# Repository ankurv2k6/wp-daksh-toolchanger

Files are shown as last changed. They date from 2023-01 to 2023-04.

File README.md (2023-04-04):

# WP-DAKSH 3D Printed Tool Changer

'WP-DAKSH' 3D Printed Tool Changer is a fully 3D printed tool changer compatible  with different CoreXY platforms like the Voron Trident, 1.8, 2.4  and RatRig VCore 3. 

It features state of the art advanced features including: 

  * Reliable tool changing mechanism powered by a single servo
  * Servo Burnout protection for enhanced life and efficient tool changes
  * Intelligent Error State Detection and Recovery minimizing failed prints
  * Automatic XYZ calibration across the different tools
  * Ultra Fast tool changing times of approx. 10 seconds - including nozzle cleaning and priming.
  * Capable of High accelerations and print speeds
  * Minimal loss in build space with the tool changer addition
  * Integrated nozzle cleaning mechanism for clean prints without the need for a purge tower / ooze shield
  * 4x4 LED Display on toolhead to display the current state of toolhead
  * Custom Klipper configuration, modules and macros for an integrated software package
  * Stiff Wire Looms and recoil management like Prusa XL - wire looms are entirely contained within the printer frame itself.
  *  Fully Enclosed Design in the same design ethos as the original Voron Trident design - giving it the ability to print high temp materials like ABS, PA6-CF and PC-CF etc which require enclosed chambers.

The design is open source and can be used freely for non commercial purposes. Do join the discord group at the link below and subscribe to the Youtube channel for more updates and interesting projects like this.

* Github - https://github.com/ankurv2k6/wp-daksh-toolchanger
* WP-Daksh Discord - https://discord.gg/Kz9VC8rWPg
* Initial BOM - https://docs.google.com/spreadsheets/d/12ISdJoCqgUTPsUwRrQ3VZWM-GBWw20C0cgHo7VGqMWU

Build Log and Demo videos 

https://www.youtube.com/channel/UCr8K1tva2CaEhyqNyaEjq_w

* Part 1 - Design Overview, Locking Mechanism & Multi Platform Compatibility
* Part 2 - Frame Overview & Carriage Assembly with Tool Locking Mechanism
* Part 3 - Assembling a tool - Dragon and V6 Hotend
* Part 4 - Putting it all together - carriage, tool, dock and their alignment 
* Part 5 - Wiring Overview - wire looms & ptfe management
* Part 6 - Electronics and Wiring management
* Part 7 - Software Setup & Initial Configuration
* Part 8 - Printing in multi material with the tool changer.

IMPORTANT INFO

Supports Needed for the following parts:

* Tools - STL/tools/v6/v6_front.stl, STL/tools/dragon/dragon_front.stl
* Dock -  STL/dock/dock_mount_left.stl, STL/dock/dock_mount_right.stl, STL/dock/dock_mount_middle.stl

Intelligent Error State Detection and Recovery Demo - https://www.youtube.com/watch?v=iPQEkaGzjxA&t=93s

Automatic XYZ Multi Tool Calibration Demo - https://www.youtube.com/watch?v=ppcTm3NfDo0

Sample Prints

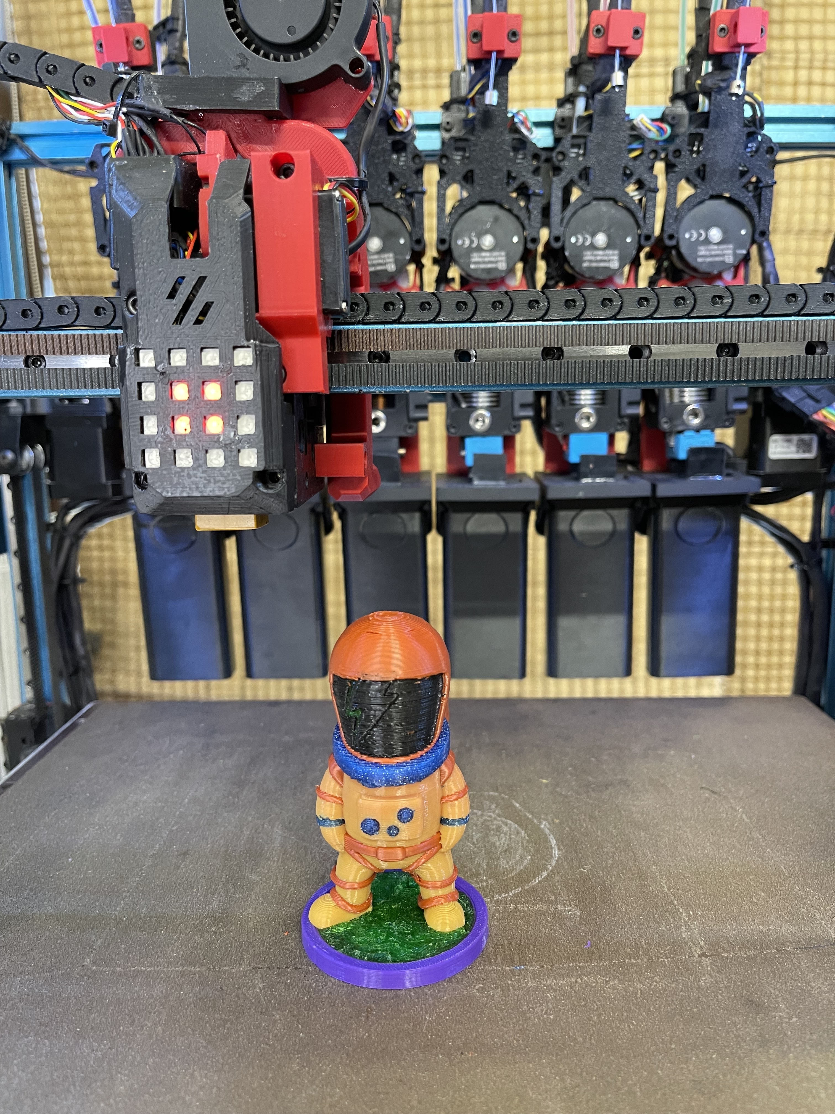
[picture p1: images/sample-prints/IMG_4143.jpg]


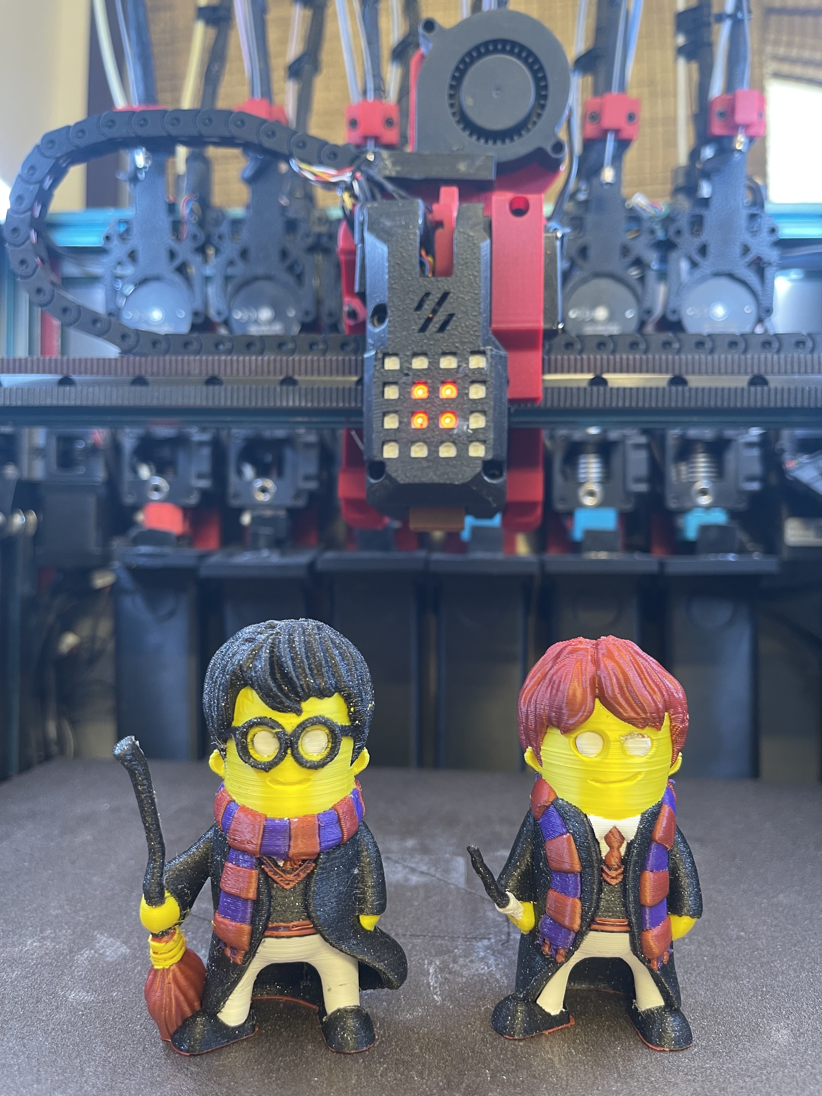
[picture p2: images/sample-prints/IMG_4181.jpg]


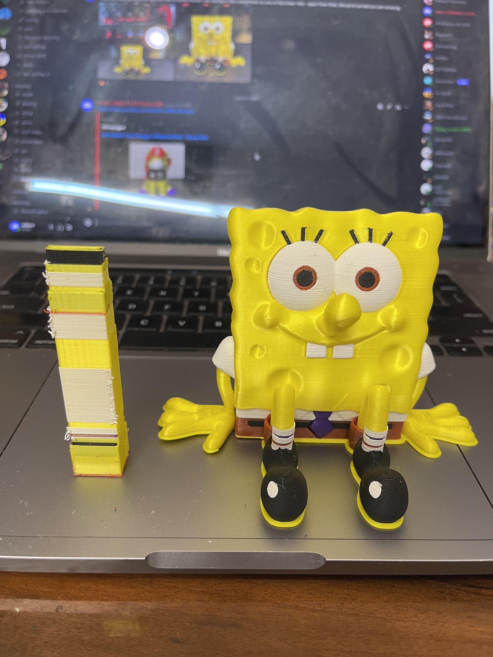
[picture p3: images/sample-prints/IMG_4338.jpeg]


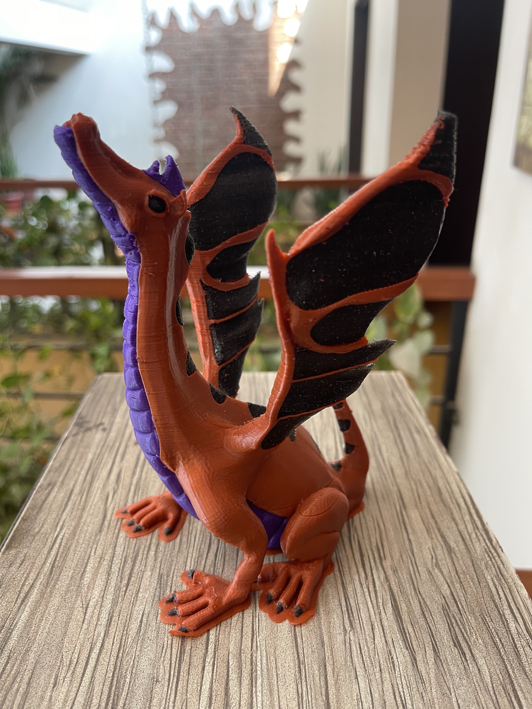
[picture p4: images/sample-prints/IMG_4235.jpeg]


Build Images

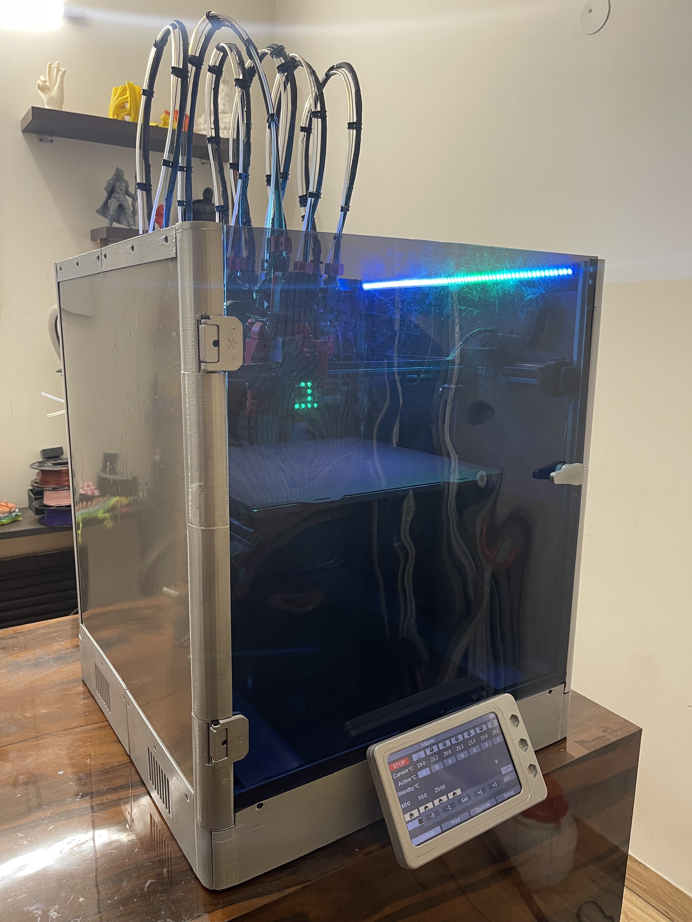
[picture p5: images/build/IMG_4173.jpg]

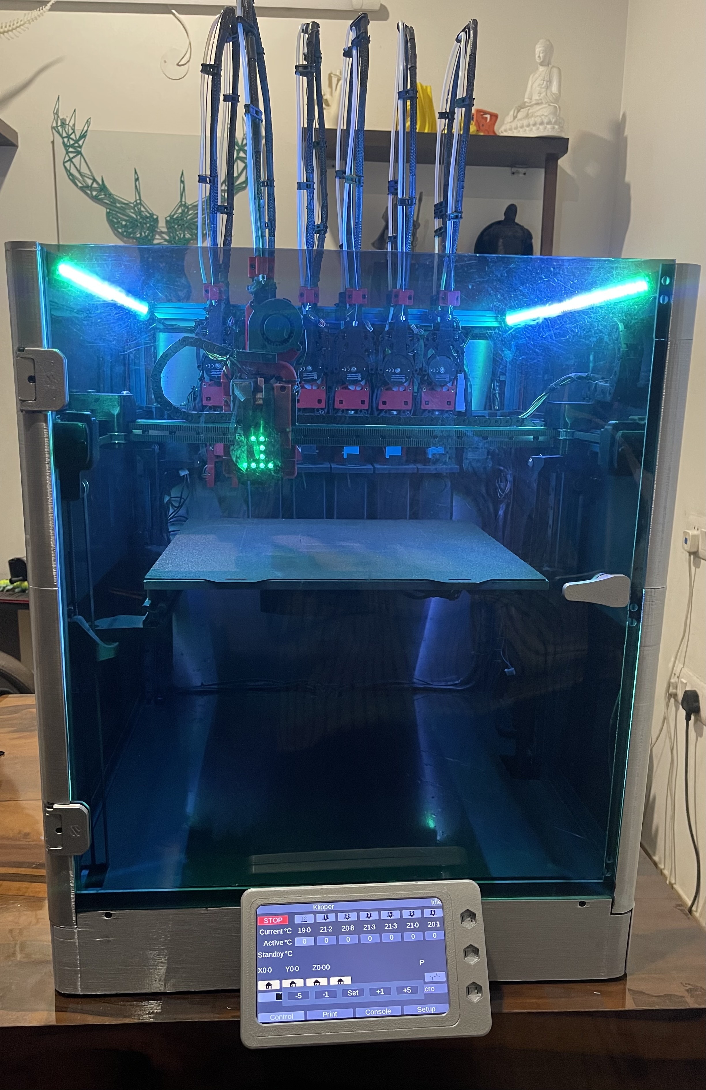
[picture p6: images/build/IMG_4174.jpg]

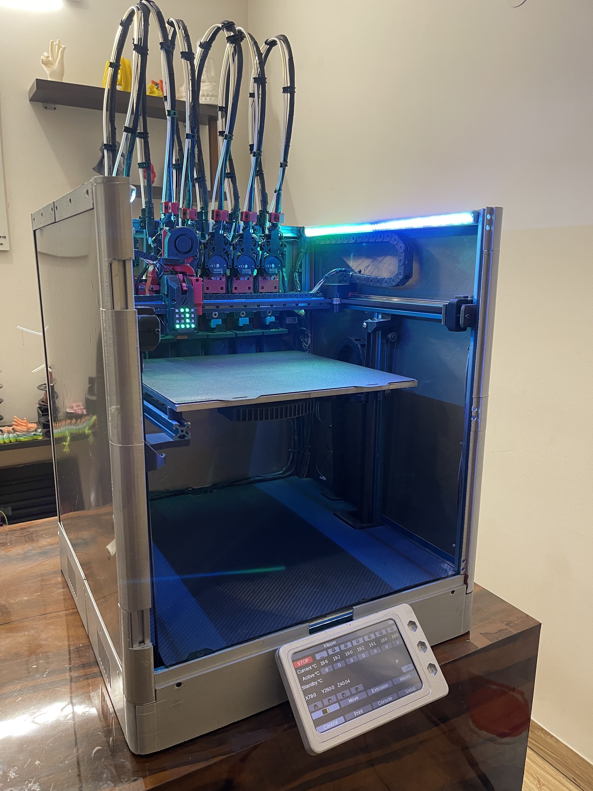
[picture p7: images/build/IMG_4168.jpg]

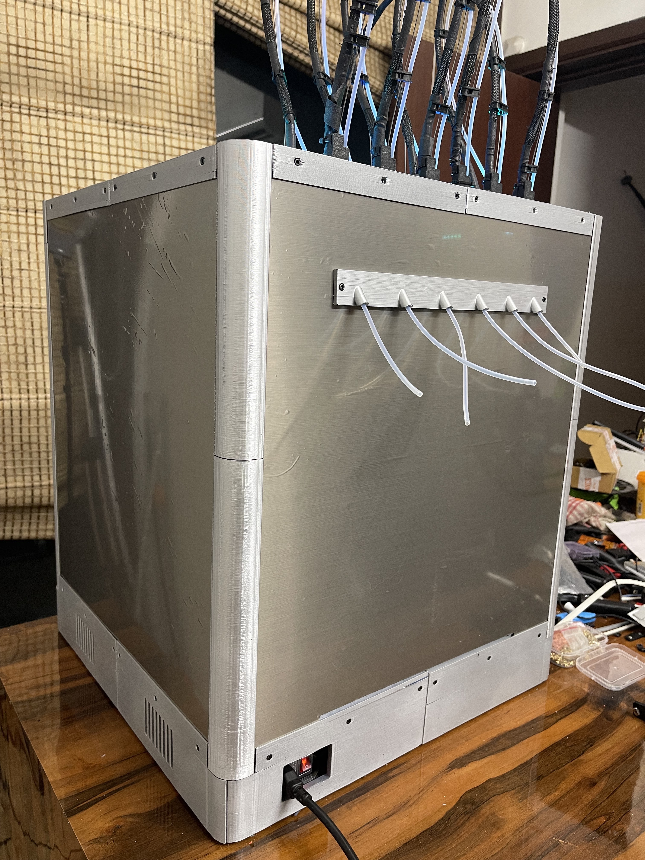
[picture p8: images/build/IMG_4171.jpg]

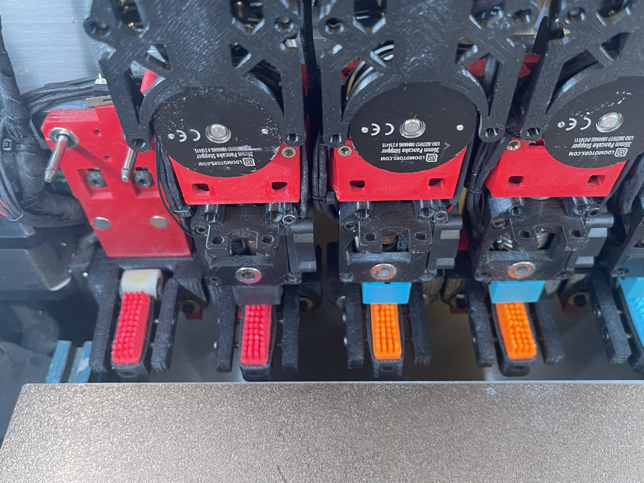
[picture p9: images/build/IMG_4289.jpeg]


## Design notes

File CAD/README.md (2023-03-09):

# WP-DAKSH 3D Printed Tool Changer - CAD Models

CAD Models are being provided due to the excellent effort of @edcasati who took it upon to convert the STLs from Tinkercad into a viable Fusion 360 Model. It might not be perfect - but its an excellent start for anyone who wants to modify the WP-DAKSH tool changer to fit their system.

Many Thanks @edcasati - really appreciate the effort.

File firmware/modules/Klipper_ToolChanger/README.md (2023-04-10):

Note: probe_multi_axis.py and atc_switch.py were dervied from the excellent work done here - https://github.com/ben5459/Klipper_ToolChanger/blob/master/probe_multi_axis.py

# Tools for klipper

This are python extras, macros and example config for the
[Klipper 3D printer firmware](https://github.com/Klipper3d/klipper). I
originally created this as macros when converting my Jubilee based
toolchanger from RRF and Duet3 to Klipper.

I welcome all contribution!

This is working great but treat it as a Beta version in development.

## Features

* **Each Tool is treated as an object and has it's own configuration** -
having configurable coordinates for parking, zoning, tool offset, 
meltzonelength, extruder, fan, etc.
*  **Multiple tools can be grouped in ToolGroup.** -Most configuration can
be inherited from the group if not specified in the tool config section.
*  **Virtual tools** - A tool can be virtual andhave a physical parent,
inheriting all nonspecified configuration from parent, parent group and
then toolgroup. Use case example of an ERCF on a PLA tool,a ERCF on a 
PETG tool, one tool without virtual tools for abrasive and yet another
tool with 3 markers that can switch between 3 markers by rotation.
* **Tools don't need to be extruders/hotends**, can be anything.
* **User defineable macro to Lock / Unlock** - Uses custom gcodes in config 
like the gcode_button. This can call a macro or multiple lines. 
* **User defineable macro to Pickup / Dropoff tools** - Can be inherited.
In the macro, `myself` refers to the calling toolobject so you can get 
myself.id for tool number or myself.offset[0] for X offset in the macro.
Ex. having same pickup gcode macro inherited for all tools from a group 
except for one that uses another type of toolwipe and has it's own pickup_gcode.
* **Global ToolLock parameters** - example purge_on_toolchange can be set 
to false when aligning tools with TAMV/ZTATP.
* **Fan speed** is carried over on toolchange if the tool has a fan. Also
`M106`/`M107` defaults to current_tool to set fan speed but can also use a Pnnn 
parameter to specify another tool.
* **Extruder temperature control** - 
  - Definable for any tool with a Pnnn parameter or defaults to current_tool
  - Has diffrent Active and Standby temperatures.
  - Can be set in Active, Standby or Off mode.
  - Can have delayed Standby and Off. Configured and/or customized with N and O parameters at runtime.
    - Example. Set Standby temperature 30 sec after putting the tool in standby and in Off after 30 minutes of not being activated.
    - Or set Time to standby to 0.1 for instant standby and Time to Powerdown to 604800 for a having it powered for a week.
    - Usefull when having sporadic toolchanges in a large print or many toolchanges in a small print.
  - Wait to reach temperature with tolerance. Set temperature +/- configurable tolerance.
* Current Tool is saved and restored at powerdown. Default but optional.
* Input shaper parameters for each tool.
* Position prior to toolchange can optionaly be saved and restored.

## Installation Instructions
### Install with Moonraker Autoupdate Support
This plugin assumes that you installed Klipper into your home directory (usually `/home/pi`). 

1) Clone this repo into your home directory where Klipper is installed:
```
cd ~
git clone https://github.com/TypQxQ/Klipper_ToolChanger.git
```

2) Edit `moonraker.conf` by adding the following entry:
```
[update_manager client klipper_toolchanger]
type: git_repo
path: ~/Klipper_ToolChanger
origin: https://github.com/TypQxQ/Klipper_ToolChanger.git
install_script: install.sh
is_system_service: False
```

3) Run the `install.sh` script
```
~/Klipper_ToolChanger/install.sh
```

Klipper_ToolChanger will show up in the update the next time you restart moonraker, or you can restart mooraker right away with: `sudo systemctl restart moonraker`.
If you encouter errors after an automatic Klipper update you can safetly run the `install.sh` scipt again to repair the links to the extension.

### Manual Install
Copy the python (`*.py`) files into the `\klipper\klipper\extras` directory. Assuming Klipper is installed in your home directory:
```
cp ./*.py ~/klipper/klippy/extras/
```
Then restart Klipper to pick up the extensions.

## To do:
* Add virtual tools select code.
* Add selectable automatic calculation of active times based on previous times. Ex:
  * Mean Layer time Standby mode. - Save time at every layerchange and at toolchange set to mean time of last 3 layers *2 or at last layer *1.5 with a Maximum and a minimum time. Needs to be analyzed further.
  * Save the time it was in Standby last time and apply a fuzzfactor. Put tool in standby and heatup with presumption that next time will be aproximatley after the same time as last. +/- Fuzzfactor.
* Save pressure avance per tool to be restored on toolchange. Also between virtual tools. Check Slicer output first if this is needed or can be put in Filament custom gcode.

## Configuration requirements
* `[input_shaper]` needs to be used for input shaper to wordk.

## G-Code commands:
* `TOOL_LOCK` - Lock command
* `TOOL_UNLOCK` - Unlock command
* `Tn` - T0, T1, T2, etc... A select command is created for each tool. 
  * `R` - Calls SAVE_CURRENT_POSITION with the variable as a RESTORE_POSITION_TYPE. For example "T0 R1" will call "SAVE_CURRENT_POSITION RESTORE_POSITION_TYPE=1" before moving. Positioned is restored with "RESTORE_POSITION" from below.
* `T_1` - Dropoff the current tool without picking up another tool
* `SET_AND_SAVE_FAN_SPEED` - Set the fan speed of specified tool or current tool if no `P` is supplied. Then save to be recovered at ToolChange.
  * `S` - Fan speed 0-255 or 0-1, default is 1, full speed.
  * `P` - Fan of this tool. Default current tool.
* `TEMPERATURE_WAIT_WITH_TOLERANCE` - Waits for all temperatures, or a specified tool or heater's temperature.
This command can be used without any additional parameters. Without parameters it waits for bed and current extruder. Only one of either TOOL or HEATER may be used.
  - `TOOL` - Tool number.
  - `HEATER` - Heater number. 0="heater_bed", 1="extruder", 2="extruder1", 3="extruder2", etc. Only works if named as default, this way.
  - `TOLERANCE` - Tolerance in degC. Defaults to 1*C. Wait will wait until heater is between set temperature +/- tolerance.
* `SET_TOOL_TEMPERATURE` - Set tool temperature.
  * `TOOL` - Tool number, optional. If this parameter is not provided, the current tool is used.
  * `STDB_TMP` - Standby temperature(s), optional
  * `ACTV_TMP` - Active temperature(s), optional
  * `CHNG_STATE` - Change Heater State, optional: 0 = off, 1 = standby temperature(s), 2 = active temperature(s).
  * `STDB_TIMEOUT` - Time in seconds to wait between changing heater state to standby and setting heater target temperature to standby temperature when standby temperature is lower than tool temperature.
    * Use for example 0.1 to change immediately to standby temperature.
  * `SHTDWN_TIMEOUT` - Time in seconds to wait from docking tool to shutting off the heater, optional.
    * Use for example 86400 to wait 24h if you want to disable shutdown timer.
* `SET_GLOBAL_OFFSET` - Set a global offset that can be applied to all tools
  * `X` / `Y` / `Z` - Set the X/Y/Z offset position
  * `X_ADJUST` / `Y_ADJUST` / `Z_ADJUST` - Adjust the X/Y/Z offset position incramentally
* `SET_TOOL_OFFSET` - Set the offset of an individual tool
  * `TOOL` - Tool number, optional. If this parameter is not provided, the current tool is used.
  * `X` / `Y` / `Z` - Set the X/Y/Z offset position
  * `X_ADJUST` /`Y_ADJUST` / `Z_ADJUST` - Adjust the X/Y/Z offset position incramentally  
* `SET_PURGE_ON_TOOLCHANGE` - Sets a global variable that can disable all purging (can be used in macros) when loading/unloading. For example when doing a TAMV/ZTATP tool alignement.
* `SAVE_POSITION` - Sets the Restore type and saves specified position for the toolhead. This command is usually used inside the custom g-code of the slicer software. The restore_position_on_toolchange_type will be changed to reflect the passed parameters.
  * X= X position to save, optional but Y must be specifie or this will be ignored.
  * Y= Y position to save, optional but X must be specifie or this will be ignored.
  * Z= Z position to save, optional but X and Y must be specifie or this will be ignored.
    * With no parameters it will set Restore type to 0, no restore.
    * With X and Y parameters it will save the specified X and Y. Sets restore type to 1, restore XY.
    * With X, Y and Z parameters it will save the specified X, Y and Z. Sets restore type to 2, restore XYZ.
* `SAVE_CURRENT_POSITION` - Save the current G-Code position of the toolhead. This command is usually used inside the pickup_gcode script or the custom g-code of the slicer software.
  * RESTORE_POSITION_TYPE= Type of restore, optional. If not specified, restore_position_on_toolchange_type will not be changed.
    * 0: No restore
    * 1: Restore XY
    * 2: Restore XYZ
* `RESTORE_POSITION` - Restore position to the latest saved position. This command is usually used inside the pickup_gcode script.
  * RESTORE_POSITION_TYPE= Type of restore, optional. If not specified, restore_position_on_toolchange_type will be used.
    * 0: No restore
    * 1: Restore XY
    * 2: Restore XYZ
## Values accesible from Macro for each object
- **Toollock**
  - `global_offset` - Global offset.
  - `tool_current` - -2: Unknown tool locked, -1: No tool locked, 0: and up are toolnames.
  - `saved_fan_speed` - Speed saved at each fanspeedchange to be recovered at Toolchange.
  - `purge_on_toolchange` - For use in macros to enable/disable purge/wipe code globaly.
  - `restore_position_on_toolchange_type` - The type of restore position:
    - 0: No restore
    - 1: Restore XY
    - 2: Restore XYZ
  - `saved_position` - The position saved when the latest T# command had a RESTORE_POSITION parameter to other than 0
- **Tool** - The tool calling this macro is referenced as `myself` in macros. When running for example `T3` to pickup the physical tool, in `pickup_gcode:` of one can write `{myself.name}` which would return `3`.
  - `name` - id. 0, 1, 2, etc.
  - `is_virtual` - If this tool has another layer of toolchange possible.
  - `physical_parent_id` - Parent physical tool that holds tool coordinates. Can be same as this.
  - `extruder` - extruder name as configured.
  - `fan` - fan name.
  - `lazy_home_when_parking` - When set to 1, will home unhomed XY axes if needed and will not move any axis if already homed and parked. 2 Will also home Z if not homed.
  - `meltzonelength` - Meltzonelength to unload/load filament at toolpak. See e3d documentation.
  - `zone` - Fast aproach coordinates when parking
  - `park` - Parking spot, slow aproach.
  - `offset` - Tool offset.
  - `heater_state` - 0 = off, 1 = standby temperature, 2 = active temperature. Placeholder.
  - `heater_active_temp` - Temperature to set when in active mode.
  - `heater_standby_temp` - Temperature to set when in standby mode.
  - `idle_to_standby_time` - Time in seconds from being parked to setting temperature to standby the temperature above. Use 0.1 to change imediatley to standby temperature.
  - `idle_to_powerdown_time` - Time in seconds from being parked to setting temperature to 0. Use something like 86400 to wait 24h if you want to disable. Requred on Physical tool.
- **ToolGroup**
  - `is_virtual` - As above
  - `physical_parent_id` - As above
  - `lazy_home_when_parking` - As above

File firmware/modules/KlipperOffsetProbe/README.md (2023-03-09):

# KlipperOffsetProbe
A Klippy plugin which solves the problem (when paired with a removable hardware probe) of finding the Z-offset between multiple tools.

If you have a toolchanger or IDEX printer you probably find yourself having to manually set Z offsets from time to time, either when changing tools or changing nozzles.

This script will cycle through each tool and probe the nozzle on a hardware probe somewhere on the printer and report the difference between the nozzle and the standard Z limit switch for each tool.

## How's it work?
When `offset_probe` is called on the printer the script will:
- Home the Z limit switch on top of the probe to get a Z0 location
- Check the config for a toolchange command named `toolchange_gcode_<tool number>` where tool number is between 0 and 99
- Executes the specified ttolchange Gcode, then moves to (`probe_x`, `probe_y`) and performs a probe using the custom probe specified by `pin` config
- Calculates the difference between the trigger of the Z probe and the custom probe to determine offset

After probing each tool the final results will be logged in the console to be saved by you.
Since toolchanging has no standardised approach in the Klipper world this is an easier approach than making assumptions about any specific implementation.

## Config example

```yaml
[offset_probe]
# Define the pin that the extra probe is connected to
pin: ^PC16
# X,Y coordinates to probe - these should be the native coordinates before any offsets are applied
probe_x: 150
probe_y: 150
# Z offset of the Z limit switch, which will be added to the calculated offset
z_offset: 0
# Additional offset added to each determined tool offset to account for micro switch pre-travel
# e.g. when using a removable hardware probe that utilises a micro switch to trigger
switch_offset: 0
# The speed (in mm/sec) to move tools down onto the probe
speed: 5
# The speed (in mm/sec) to retract between probes
lift_speed: 5
# Distance to retract between probes - default of 0.5
lift_distance: 10
# The speed (in mm/sec) of X/Y moves - default of 100
move_speed: 100
# Gcode macro to be run before anything else happens. A good use might be to ensure no tools are attached
start_gcode:
    TOOL_DROPOFF
# Gcode macro to run after all tools are probed, for example to ensure all tools were parked
end_gcode:
    TOOL_DROPOFF
# Defines 3 tools to be probed. Note that they do not have to be sequential, you may skip tools if that's desirable
toolchange_gcode_0:
    T0
toolchange_gcode_1:
    T1
toolchange_gcode_2:
    T2
```

## Installation
The simplest maintainable approach is to clone this repo to your host and then link the script to the klippy folder:
```bash
git clone https://github.com/Xonman/KlipperOffsetProbe ~/KlipperOffsetProbe
ln -s ~/KlipperOffsetProbe/offset_probe.py ~/klipper/klippy/extras/offset_probe.py
```
This should allow you to pull updates to the script without having to copy/paste it into the klippy folder each time.

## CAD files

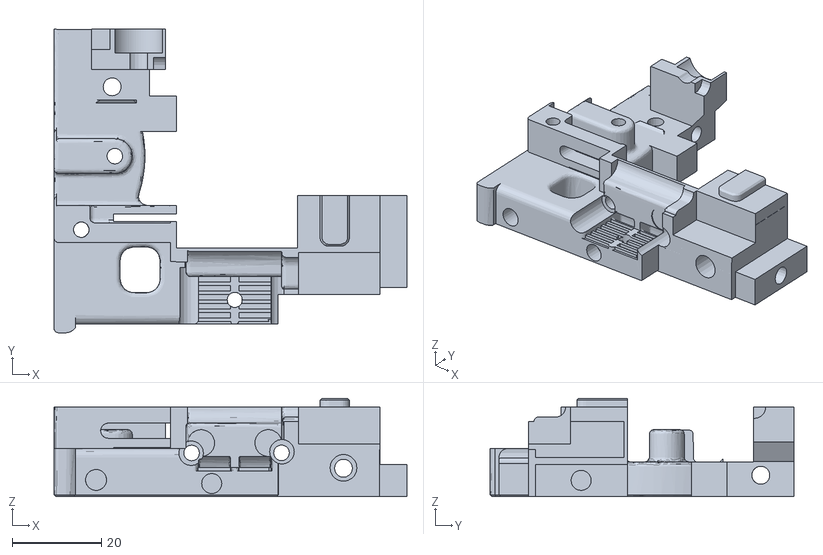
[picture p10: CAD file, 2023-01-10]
STL/carriage/carriage_right.stl
78.9 x 67.9 x 22.0

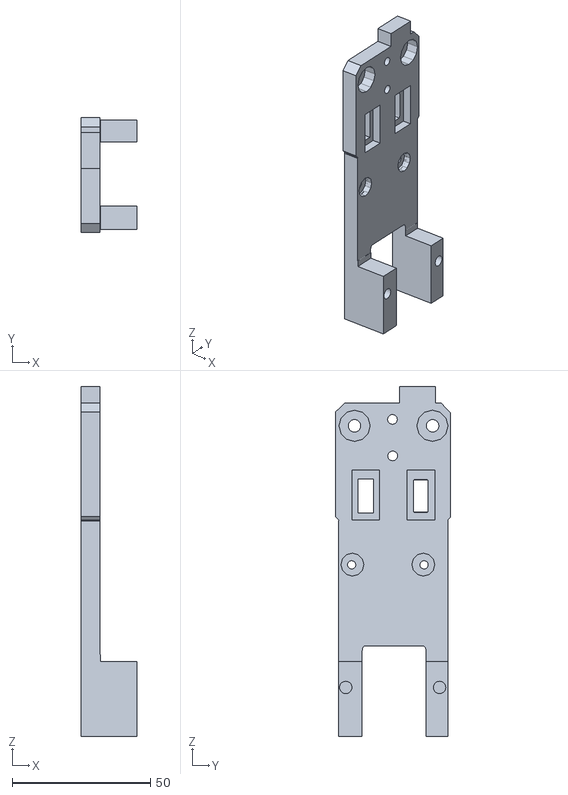
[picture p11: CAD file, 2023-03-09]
STL/dock/nozzle_wiper_mount.stl
20.1 x 41.7 x 126.6

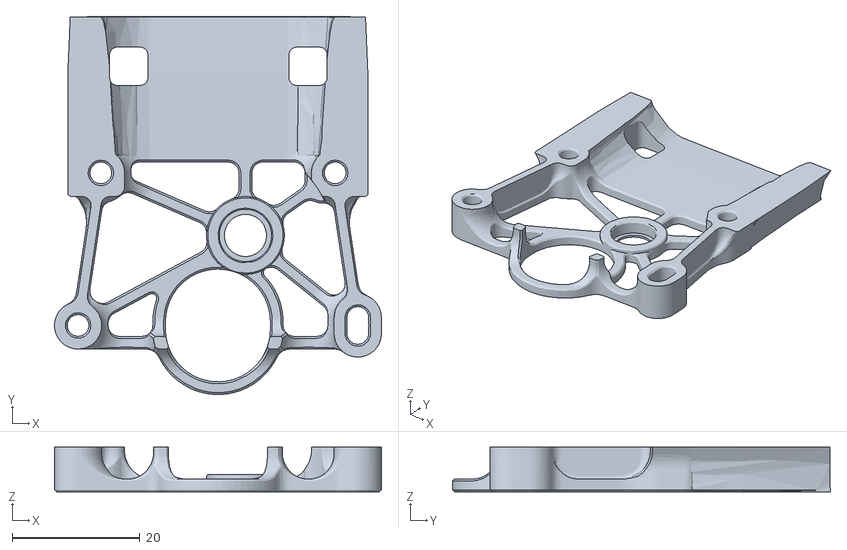
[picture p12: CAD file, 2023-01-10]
STL/extruder/extruder_back.stl
51.2 x 59.2 x 7.00

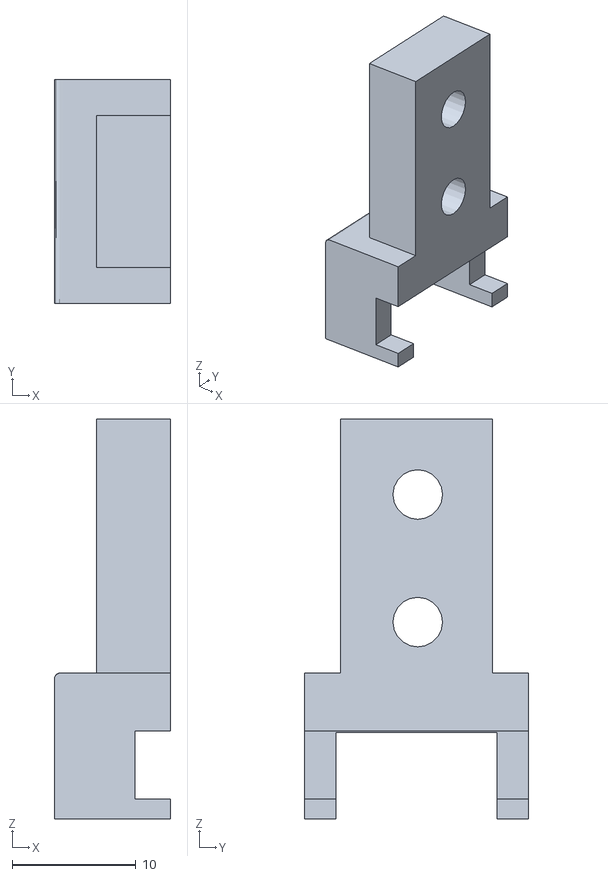
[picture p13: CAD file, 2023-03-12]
STL/front_idlers_25mm_extra_Y/y-endstop.stl
9.40 x 18.1 x 32.3

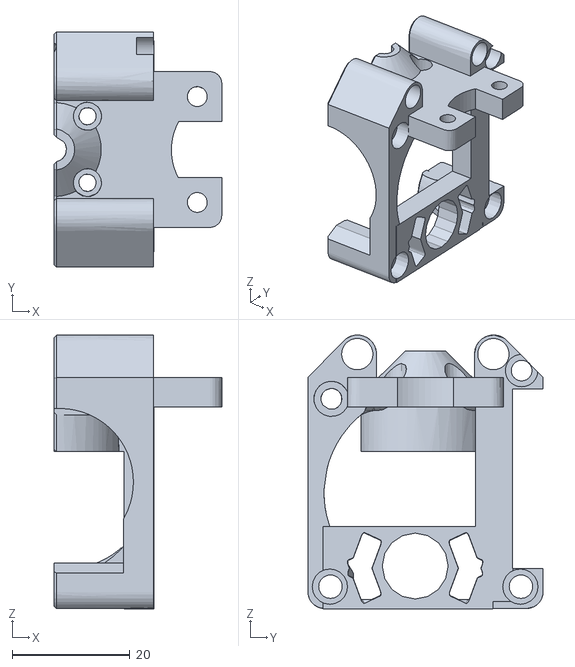
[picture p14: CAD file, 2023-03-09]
STL/tools/tool_dragon/dragon_front.stl
28.5 x 40.0 x 46.6

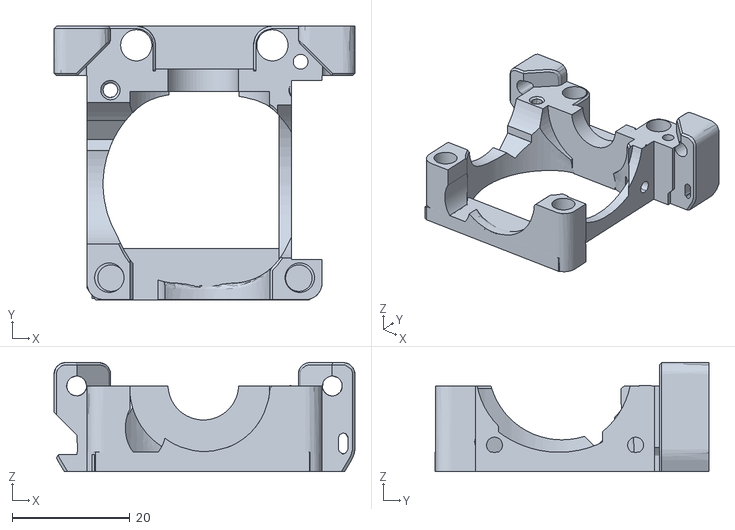
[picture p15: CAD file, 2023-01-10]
STL/tools/tool_v6/v6_back.stl
51.2 x 46.5 x 18.5

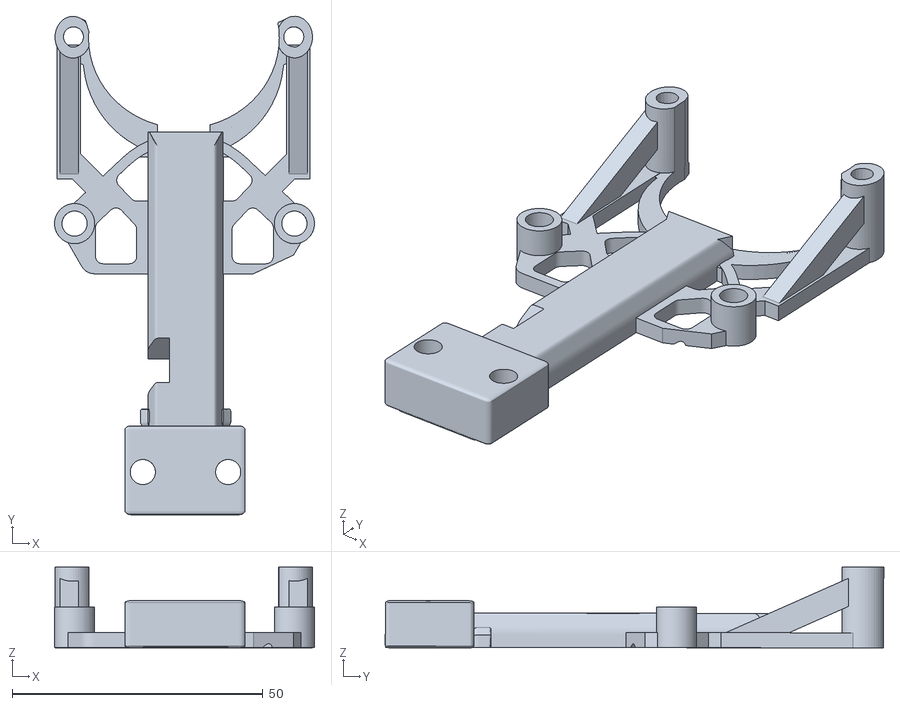
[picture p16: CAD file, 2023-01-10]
STL/umbilical/tool_umbilical_mount.stl
51.8 x 99.3 x 16.1

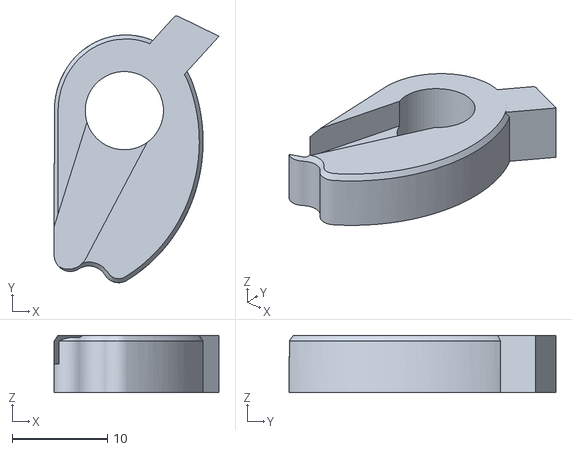
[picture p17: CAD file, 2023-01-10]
STL/carriage/servo_horn.stl
17.3 x 28.0 x 6.01

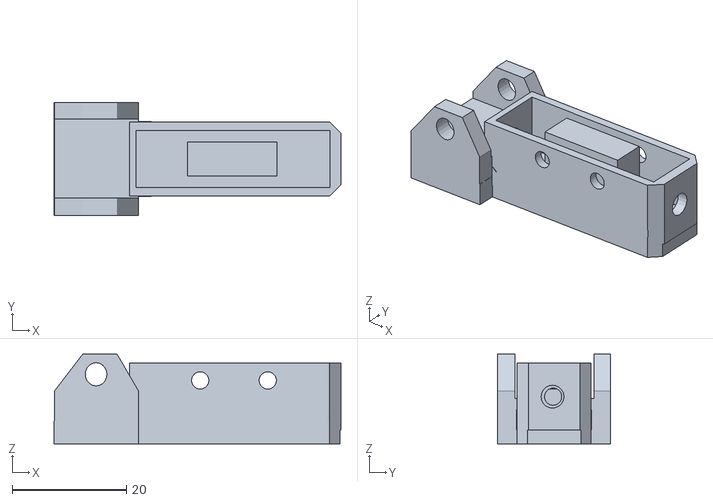
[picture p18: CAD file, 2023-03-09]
STL/dock/ooze_shield_nozzle_wiper.stl
50.1 x 19.8 x 15.7

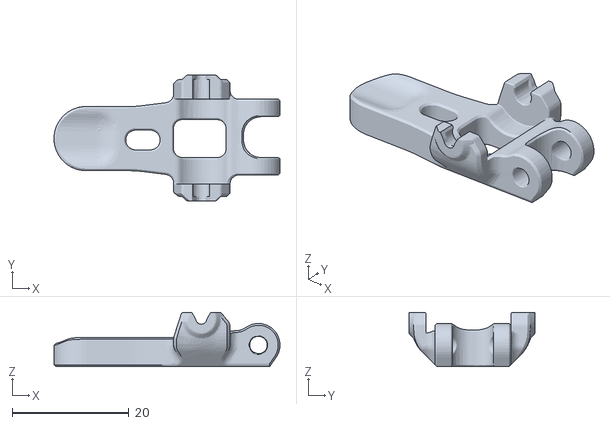
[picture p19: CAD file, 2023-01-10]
STL/extruder/extruder_idler.stl
38.7 x 21.6 x 9.30

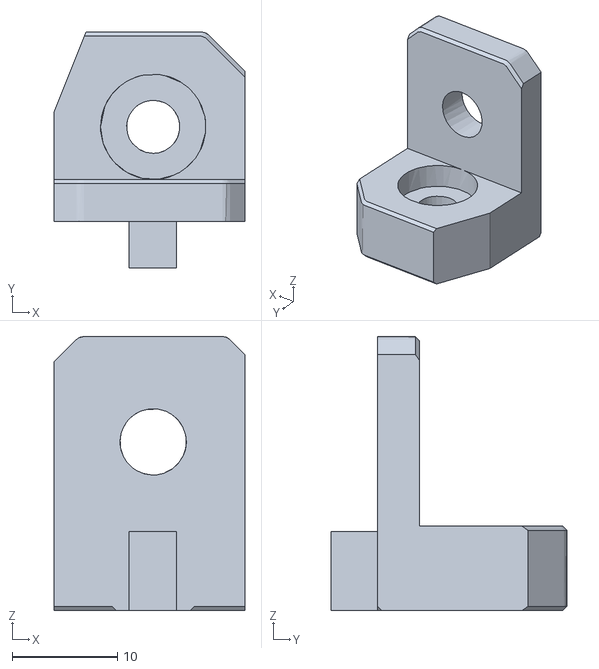
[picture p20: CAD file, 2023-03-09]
STL/front_idlers_25mm_extra_Y/left_top.stl
18.1 x 22.4 x 26.0

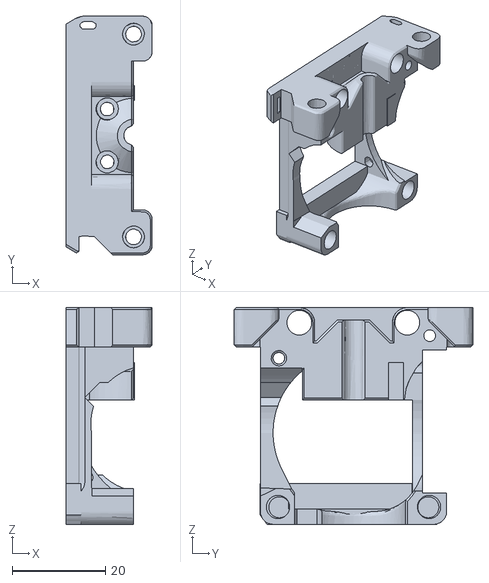
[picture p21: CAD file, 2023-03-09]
STL/tools/tool_dragon/dragon_back.stl
18.5 x 51.2 x 46.5

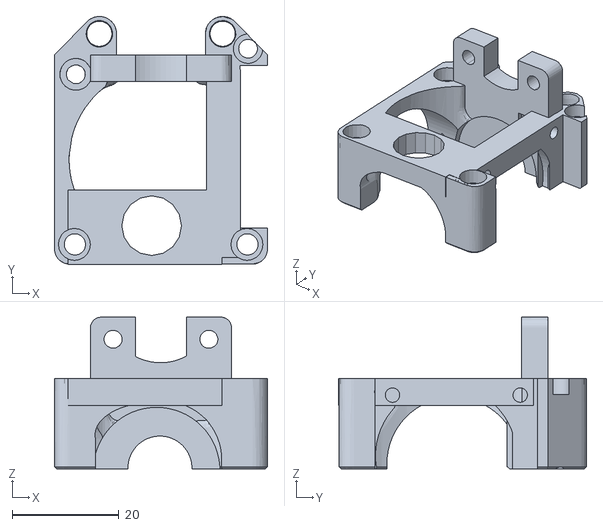
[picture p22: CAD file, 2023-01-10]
STL/tools/tool_v6/v6_front.stl
40.0 x 46.6 x 28.5

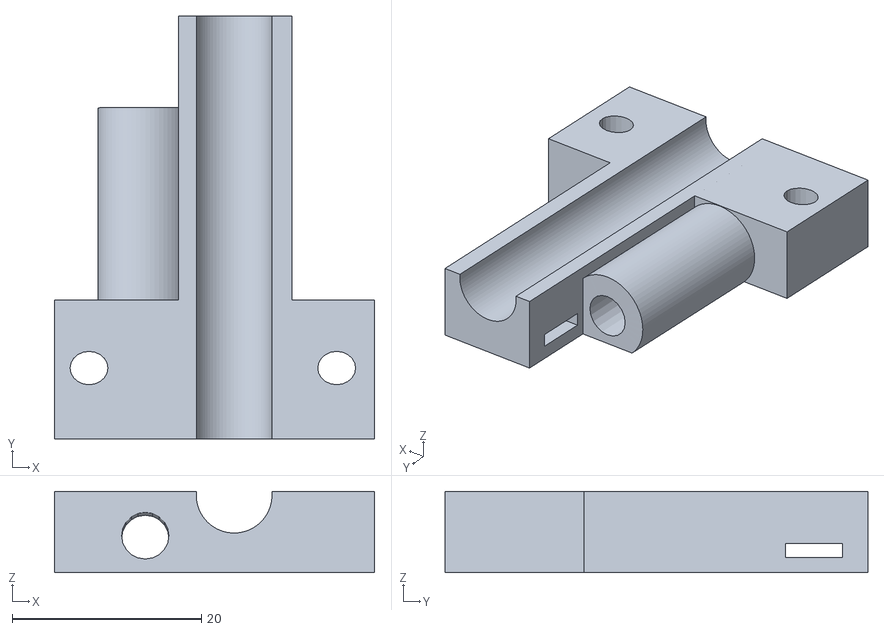
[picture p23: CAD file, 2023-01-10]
STL/umbilical/umbilical_extrusion_mount.stl
33.8 x 44.7 x 8.60

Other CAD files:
STL/carriage/toollocking_pushrod.stl
STL/dock/dock_mount_middle.stl
STL/extruder/extruder_bearing_holder.stl
STL/front_idlers_25mm_extra_Y/left_z_idler.stl
STL/carriage/carriage_left.stl
STL/carriage/front_cowling_led_matrix.stl
STL/carriage/front_cowling_logo.stl
STL/carriage/partfan_left.stl
STL/carriage/partfan_right.stl
STL/carriage/partfan_top.stl
STL/carriage/servo_1.stl
STL/carriage/servo_2.stl
STL/carriage/toolchanger_camshaft.stl
STL/carriage/toollocking_left.stl
STL/carriage/toollocking_nozzle_holder.stl
STL/carriage/toollocking_right.stl
STL/dock/deprecated/dock_wiper_bin.stl
STL/dock/deprecated/dock_wiper_mount.stl
STL/dock/dock_body.stl
STL/dock/dock_mount_left.stl
STL/dock/dock_mount_right.stl
STL/extruder/extruder_front.stl
STL/front_idlers_25mm_extra_Y/left_bottom.stl
STL/front_idlers_25mm_extra_Y/left_middle.stl
STL/front_idlers_25mm_extra_Y/right_bottom.stl
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

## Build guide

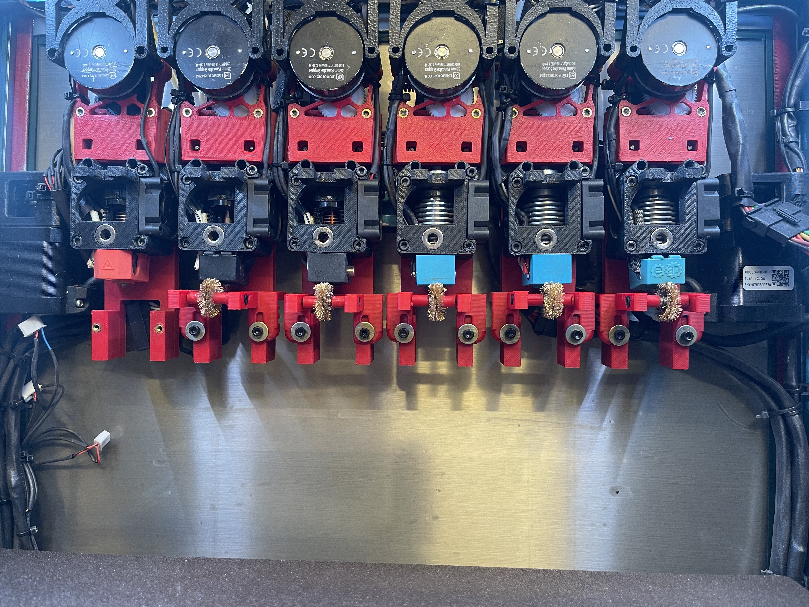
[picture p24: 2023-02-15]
images/build/IMG_4190.jpg

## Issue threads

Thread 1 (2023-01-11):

Hi, great project, fusion file / step file share?

izanamisu, 2023-01-11:
Hi, great work on your project,

I am trying to try out your design in a custom voron printer (V2.4+belted trident combo) but i can only find stl files (STL sucks..) I see you use fusion 360 https://www.youtube.com/watch?v=ngXJsfzE4eQ&ab_channel=3DUnplugged
can you please share the fusion / step files?

jhandel, 2023-01-12:
Second this request for STEP files, I am looking at building a Voron 2.4 so these will likely need tweaks.

HenryJia, 2023-01-21:
Thirds this, I am also using a 2.4 and will undoubtedly want to make changes to make this work for that

ankurv2k6, 2023-01-22:
Hi - the CAD files is being worked on and will be available shortly.

ankurv2k6, 2023-03-10:
The CAD file is now available in the repository.

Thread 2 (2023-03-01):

Automatic XYZ Multi Tool Calibration

easycorexy, 2023-03-01:
Hi,

This is a great project!

How did you programmed the Automatic XYZ Multi Tool Calibration?

I find it very interesting.

easycorexy, 2023-04-04:
Thank you very much for your answer.

How does the printer 'know' that it came in contact with the object? Is there any strain sensor on the hotend? Or the whole thing relays on the sensorless homing?

Fyi: I'm building an IDEX 3d printer and what to make the XY offset calibration between the 2 printheads automatically.

Best Regards,
Dan

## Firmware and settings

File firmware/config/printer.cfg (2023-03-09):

# This file contains common pin mappings for the BigTreeTech GTR.
# To use this config, the firmware should be compiled for the
# STM32F407 with a "32KiB bootloader".

# The "make flash" command does not work on the GTR. Instead,
# after running "make", copy the generated "klipper/out/klipper.bin" file to a
# file named "firmware.bin" on an SD card and then restart the GTR
# with that SD card.

# See docs/Config_Reference.md for a description of parameters.

[include toolchanger.cfg]

[skew_correction] 
[exclude_object]

[mcu]
serial: /dev/serial/by-id/usb-Klipper_stm32f446xx_25000B000E5053424E363620-if00

[mcu mcu1]
serial: /dev/serial/by-id/usb-Klipper_lpc1769_0A60011125813AAFC3CA6B5CC12000F5-if00

[printer]
kinematics: corexy
max_velocity: 400
max_accel: 8000
max_z_velocity: 300
max_z_accel: 500
square_corner_velocity: 5.0  

[thermistor Trianglelab NTC100K B3950]
## values calibrated against a PT100 reference
temperature1: 25.0
resistance1: 103180.0
temperature2: 150.0
resistance2: 1366.2
temperature3: 250.0
resistance3: 168.6

[pause_resume]

[display_status]

#[exclude_object]

[virtual_sdcard]
path: /home/pi/printer_data/gcodes


[mcu rpi]
serial: /tmp/klipper_host_mcu

#[adxl345]
#cs_pin: rpi:None

#[resonance_tester]
#accel_chip: adxl345
#probe_points:
#    160,175,40  # an example

[stepper_x]
step_pin: PF13
dir_pin: PF12
enable_pin: !PF14
microsteps:64
rotation_distance: 40
full_steps_per_rotation: 200
endstop_pin: mcu1:P1.29
position_min: 0
position_endstop: 0
position_max: 320
homing_speed: 50
homing_retract_dist: 5
second_homing_speed: 5
homing_positive_dir: false


[stepper_y]
step_pin: PG0
dir_pin: !PG1
enable_pin: !PF15
microsteps: 64
rotation_distance: 40
full_steps_per_rotation: 200
endstop_pin: mcu1:P1.28
position_endstop: 0
position_max: 330
position_min: 0
homing_speed: 50
homing_retract_dist: 5
second_homing_speed: 5
homing_positive_dir: false



[stepper_z]
step_pin: PF9
dir_pin: PF10
enable_pin: !PG2
rotation_distance: 40			# 20T pulley driving bed, 2mm belt pitch
gear_ratio: 80:16				# 16T pulley on stepper, 80T gear
microsteps: 32
full_steps_per_rotation: 200	#200 for 1.8 degree, 400 for 0.9 degree
endstop_pin: probe:z_virtual_endstop
position_max: 300
position_min: -5
homing_speed: 75
second_homing_speed: 1


[stepper_z1]
step_pin: PG4
dir_pin: PC1
enable_pin: !PA0
rotation_distance: 40			# 20T pulley driving bed, 2mm belt pitch
gear_ratio: 80:16				# 16T pulley on stepper, 80T gear
microsteps: 32
full_steps_per_rotation: 200	#200 for 1.8 degree, 400 for 0.9 degree


[stepper_z2]
step_pin: PF11
dir_pin: !PG3
enable_pin: !PG5
rotation_distance: 40			# 20T pulley driving bed, 2mm belt pitch
gear_ratio: 80:16				# 16T pulley on stepper, 80T gear
microsteps: 32
full_steps_per_rotation: 200	#200 for 1.8 degree, 400 for 0.9 degree


[extruder]
step_pin: mcu1:P2.13
dir_pin: !mcu1:P0.11
enable_pin: !mcu1:P2.12
heater_pin: PA2 # Heat0
sensor_pin:  PF3 # T0 Header
sensor_type: Trianglelab NTC100K B3950
rotation_distance: 22.45
gear_ratio:50:10
microsteps: 32
nozzle_diameter: 0.400
filament_diameter: 1.75
min_temp: 0
max_temp: 300
max_power: 1.0
min_extrude_temp: 170
pressure_advance: 0.0395
pressure_advance_smooth_time: 0.040
max_extrude_only_distance: 250
max_extrude_cross_section: 20



[extruder1]
step_pin: PE2
dir_pin: PE3
enable_pin: !PD4
heater_pin: PA3 # Heat0
sensor_pin:  PF4 # T0 Header
sensor_type: Trianglelab NTC100K B3950
#control: pid
rotation_distance: 21.34
gear_ratio: 50:10
microsteps: 32
nozzle_diameter: 0.400
filament_diameter: 1.75
min_temp: 0
max_temp: 300
max_power: 1.0
min_extrude_temp: 170
##	Try to keep pressure_advance below 1.0
pressure_advance: 0.0395
##	Default is 0.040, leave stock
pressure_advance_smooth_time: 0.040
max_extrude_only_distance: 250
#pid_Kp: 22.2
#pid_Ki: 1.08
#pid_Kd: 114
max_extrude_cross_section: 20




[extruder2]
step_pin: PE6
dir_pin: !PA14
enable_pin: !PE0
heater_pin: PB10 # Heat0
sensor_pin:  PF5 # T0 Header
sensor_type: Trianglelab NTC100K B3950
#control: pid
rotation_distance: 22.25
gear_ratio: 50:10
microsteps: 16
nozzle_diameter: 0.400
filament_diameter: 1.75
min_temp: 0
max_temp: 300
max_power: 1.0
min_extrude_temp: 170
##	Try to keep pressure_advance below 1.0
pressure_advance: 0.0395
##	Default is 0.040, leave stock
pressure_advance_smooth_time: 0.040
max_extrude_only_distance: 250
#pid_Kp: 22.2
#pid_Ki: 1.08
#pid_Kd: 114
max_extrude_cross_section: 20


[extruder4]
step_pin: mcu1:P0.19
dir_pin: mcu1:P0.20
enable_pin: !mcu1:P2.8
heater_pin: PA1 # Heat0
sensor_pin:  PF6 # T0 Header
sensor_type: Trianglelab NTC100K B3950
#control: pid
rotation_distance: 21.80
gear_ratio: 50:10
microsteps: 16
nozzle_diameter: 0.400
filament_diameter: 1.75
min_temp: 0
max_temp: 300
max_power: 1.0
min_extrude_temp: 170
##	Try to keep pressure_advance below 1.0
pressure_advance: 0.0395
##	Default is 0.040, leave stock
pressure_advance_smooth_time: 0.040
max_extrude_only_distance: 250
#pid_Kp: 22.2
#pid_Ki: 1.08
#pid_Kd: 114
max_extrude_cross_section: 20



[extruder3]
step_pin: mcu1:P2.2
dir_pin: mcu1:P2.6
enable_pin: !mcu1:P2.1
sensor_pin: PF7
heater_pin: PB11 # Heat0
sensor_type: Trianglelab NTC100K B3950
#control: pid
rotation_distance: 22.25
gear_ratio:50:10
microsteps: 16
nozzle_diameter: 0.400
filament_diameter: 1.75
min_temp: 0
max_temp: 300
max_power: 1.0
min_extrude_temp: 170
##	Try to keep pressure_advance below 1.0
pressure_advance: 0.0395
##	Default is 0.040, leave stock
pressure_advance_smooth_time: 0.040
max_extrude_only_distance: 250
#pid_Kp: 22.2
#pid_Ki: 1.08
#pid_Kd: 114
max_extrude_cross_section: 20

[extruder5]
step_pin: mcu1:P0.22
dir_pin: !mcu1:P2.11
enable_pin: !mcu1:P0.21
heater_pin: mcu1:P2.7 # Heat0
sensor_pin: mcu1:P0.24
sensor_type: Trianglelab NTC100K B3950
#control: pid
rotation_distance: 21.5
gear_ratio: 50:10
microsteps: 16
nozzle_diameter: 0.400
filament_diameter: 1.75
min_temp: 0
max_temp: 300
max_power: 1.0
min_extrude_temp: 170
##	Try to keep pressure_advance below 1.0
pressure_advance: 0.0395
##	Default is 0.040, leave stock
pressure_advance_smooth_time: 0.040
max_extrude_only_distance: 250
#pid_Kp: 22.2
#pid_Ki: 1.08
#pid_Kd: 114
max_extrude_cross_section: 20



[verify_heater extruder]
max_error: 180
check_gain_time: 180
heating_gain: 2


[verify_heater extruder1]
max_error: 180
check_gain_time: 180
heating_gain: 2

[verify_heater extruder2]
max_error: 180
check_gain_time: 180
heating_gain: 2

[verify_heater extruder3]
max_error: 180
check_gain_time: 180
heating_gain: 2

[verify_heater extruder4]
max_error: 180
check_gain_time: 180
heating_gain: 2

[verify_heater extruder5]
max_error: 180
check_gain_time: 180
heating_gain: 2

########################################
# tmc2209 configuration
########################################

[tmc2209 stepper_x]
uart_pin: PC4
run_current: 1.1
interpolate: True
sense_resistor: 0.110
stealthchop_threshold: 0


[tmc2209 stepper_y]
uart_pin: PD11
run_current: 1.1
interpolate: True
sense_resistor: 0.110
stealthchop_threshold: 0


[tmc2209 stepper_z]
uart_pin: PF2
run_current: 0.800
interpolate: True
sense_resistor: 0.110
stealthchop_threshold: 0


[tmc2209 stepper_z1]
uart_pin: PC7
run_current: 0.800
interpolate: True
sense_resistor: 0.110
stealthchop_threshold: 0


[tmc2209 stepper_z2]
uart_pin: PC6
run_current: 0.800
interpolate: True
sense_resistor: 0.110
stealthchop_threshold: 0


[tmc2209 extruder]
uart_pin: mcu1:P1.4
run_current: 0.350
interpolate: False
sense_resistor: 0.110
stealthchop_threshold:0


[tmc2209 extruder1]
uart_pin: PE1
run_current: 0.35
interpolate: False
sense_resistor: 0.110
stealthchop_threshold: 0

[tmc2209 extruder2]
uart_pin: PD3
run_current: 0.350
interpolate: False
sense_resistor: 0.110
stealthchop_threshold: 0

[tmc2209 extruder3]
uart_pin: mcu1:P1.9
run_current: 0.350
interpolate: False
sense_resistor: 0.110
stealthchop_threshold: 0

[tmc2209 extruder4]
uart_pin: mcu1:P1.10
run_current: 0.350
interpolate: False
sense_resistor: 0.110
stealthchop_threshold: 0

[tmc2209 extruder5]
uart_pin: mcu1:P1.8
run_current: 0.350
interpolate: False
sense_resistor: 0.110
stealthchop_threshold: 0
#####################################################################
# 	FANS
#####################################################################
[fan]
pin: mcu1:P2.3 # Parts Fan


[heater_fan hotend_fan]
##	Hotend Fan - XYE board, HE1 Connector
pin: PA8
max_power: 1.0
heater: extruder
heater_temp: 100.0
fan_speed: 1.0

[heater_fan hotend_fan1]
##	Hotend Fan - XYE board, HE1 Connector
pin: PE5
max_power: 1.0
heater: extruder1
heater_temp: 100.0
fan_speed: 1.0

[heater_fan hotend_fan2]
##	Hotend Fan - XYE board, HE1 Connector
pin: PD12
max_power: 1.0
heater: extruder2
heater_temp: 100.0
fan_speed: 1.0

[heater_fan hotend_fan4]
##	Hotend Fan - XYE board, HE1 Connector
pin: PD13
max_power: 1.0
heater: extruder4
heater_temp: 100.0
fan_speed: 1.0

[heater_fan hotend_fan3]
##	Hotend Fan - XYE board, HE1 Connector
pin: PD14
max_power: 1.0
heater: extruder3
heater_temp: 100.0
fan_speed: 1.0
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

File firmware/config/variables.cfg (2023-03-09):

[Variables]
t0_x_offset = 0.0
t0_y_offset = 0.0
t0_z_offset = 0.03
t1_x_offset = 0.09687500004002914
t1_y_offset = 1.6718749999608065
t1_z_offset = 0.2083333333505266
t2_x_offset = 0.4359375000795751
t2_y_offset = -0.020312500084315843
t2_z_offset = 0.04166666670506345
t3_x_offset = 0.2687500001180069
t3_y_offset = 0.9874999998620808
t3_z_offset = -0.14041666661096386
t4_x_offset = 0.5562500001562967
t4_y_offset = 0.44062499981933456
t4_z_offset = 0.2695833334060964
t5_x_offset = 0.3609375001941544
t5_y_offset = 0.6765624997785835
t5_z_offset = 0.17458333342352716
tool_current = 2

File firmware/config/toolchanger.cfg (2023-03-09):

# Config order: ToolGroups must come before tools that use them. Tool that are used as physical_parent must be configured before other virtual tools that use that as parent.

[respond]

[include matrix_display.cfg]
[include xyz_offset_probe.cfg]
[include motor_torque.cfg]
[include intelligent_error_detection.cfg]
[include servo_macros.cfg]
[include tool_usage.cfg]
[include tool_macros.cfg]
[include toolchange_management.cfg]
[include filament_sensors.cfg]

[include slack_notifications.cfg]
[include timelapse.cfg]

[include delayed_gcode.cfg]


# Enables saving of variables between powerdown of machine. Must be configured before [toollock].
[save_variables]
filename:  ~/printer_data/config/variables.cfg



#######################
##  TOOLS CONFIG     ##
#######################

[atc_switch 0]
pin:PG13
press:
	#M118 0 PRESSED
release:
	#M118 0 RELEASE

[atc_switch 1]
pin:PG6
press:
	#M118 1 PRESSED
release:
	#M118 1 RELEASE

[atc_switch 2]
pin:PG12
press:
	#M118 2 PRESSED
release:
	#M118 2 RELEASE

[atc_switch 3]
pin:PG14
press:
	#M118 3 PRESSED
release:
	#M118 3 RELEASE

[atc_switch 4]
pin:PG15
press:
	#M118 4 PRESSED
release:
	#M118 4 RELEASE

[atc_switch 5]
pin:PG9
press:
	#M118 5 PRESSED
release:
	#M118 5 RELEASE


[atc_switch carriage]
pin:mcu1:P1.25
press:
	#M118 C PRESSED
release:
	#M118 C RELEASE



[toollock]
purge_on_toolchange = True          # Here we can disable all purging. When disabled it overrides all other purge options. Defaults to true. This can be turned off by a macro for automatic probing hot tools without probing them. For example when doing TAMV or ZTATP.
LogLevel = 0                        # How much debugging text to print to console. 0=minimum, 1=some, 2=all.
init_printer_to_last_tool = True   #Initialise as it was turned off, unlock tool if none was loaded or lock if one was loaded. Defaults to True
tool_lock_gcode:
	SAVE_GCODE_STATE NAME=tool_unlock_state                                         # Save gcode state
	{% if printer["gcode_macro CLAMP_STATUS"].clamp_status|int == 1 %}
		#SERVO_TURN_ON
		G4 P100
		SET_SERVO SERVO=clamp ANGLE=0
		SET_GCODE_VARIABLE MACRO=CLAMP_STATUS VARIABLE=clamp_status VALUE=0
		G4 P600
		#SERVO_TURN_OFF
		SET_SERVO SERVO=clamp width=0
	{% endif %}
	RESTORE_GCODE_STATE NAME=tool_unlock_state MOVE=0                               # Restore gcode state
	#M118 "Unknown tool Loaded"                                                      # Tool Loaded Message that stays on display.

tool_unlock_gcode:
	SAVE_GCODE_STATE NAME=tool_lock_state                                           # Save gcode state
	{% if printer["gcode_macro CLAMP_STATUS"].clamp_status|int == 0 %}
		#SERVO_TURN_ON
		G4 P100
		SET_SERVO SERVO=clamp ANGLE=160
		SET_GCODE_VARIABLE MACRO=CLAMP_STATUS VARIABLE=clamp_status VALUE=1
		
		G4 P600
		#SERVO_TURN_OFF
		SET_SERVO SERVO=clamp width=0
	{% endif %}
	RESTORE_GCODE_STATE NAME=tool_lock_state MOVE=0                                 # Restore gcode state
	#M118 Tool Unloaded                                                              # Tool UnLoaded Message that stays on display.


# Used to group several tools with similar settings.
[toolgroup 0]
is_virtual: False            # If True then must have a physical_parent declared and shares extruder, hotend and fan with the physical_parent
pickup_gcode: 
  SUB_TOOL_PICKUP_START T={myself.name}
  SUB_TOOL_PICKUP_END T={myself.name}

dropoff_gcode:
  SUB_TOOL_DROPOFF_START T={myself.name}
  SUB_TOOL_DROPOFF_END T={myself.name}

##### Selectable tool. Must be configured after [toolgroup n].
[tool 0]
tool_group: 0                     # Must be used and configured before this tool
extruder: extruder
zone: 150,120
park: 22,326.8
meltzonelength: 28 #18                 # Defaults to 0
idle_to_standby_time: 0.1          # Time in seconds from being parked to setting temperature to standby the temperature above. Use 0.1 to change imediatley to standby temperature. Defaults to 30
#idle_to_powerdown_time: 600       # Time in seconds from being parked to setting temperature to 0. Use something like 86400 to wait 24h if you want to disable. Defaults to 600
lazy_home_when_parking: 1           # (default: 0 - disabled) - When set to 1, will home unhomed XY axes if needed and will not move any axis if already homed and parked. 2 Will also home Z if not homed.
#shaper_freq_x: 137.2
#shaper_freq_y: 116.4
#shaper_type_x: 2hump_ei
#shaper_type_y: 2hump_ei
extra_extrude_mm: 0.25

[tool 1]
tool_group: 0                     # Must be used and configured before this tool
extruder: extruder1
zone: 150,120
park: 78,327
meltzonelength: 28 #18                 # Defaults to 0
idle_to_standby_time: 0.1          # Time in seconds from being parked to setting temperature to standby the temperature above. Use 0.1 to change imediatley to standby temperature. Defaults to 30
#idle_to_powerdown_time: 300       # Time in seconds from being parked to setting temperature to 0. Use something like 86400 to wait 24h if you want to disable. Defaults to 600
lazy_home_when_parking: 1           # (default: 0 - disabled) - When set to 1, will home unhomed XY axes if needed and will not move any axis if already homed and parked. 2 Will also home Z if not homed.
extra_extrude_mm: 0.25

[tool 2]
tool_group: 0                     # Must be used and configured before this tool
extruder: extruder2
zone: 150,120
park: 133.2,327.2
meltzonelength: 28 #18                 # Defaults to 0
idle_to_standby_time: 0.1          # Time in seconds from being parked to setting temperature to standby the temperature above. Use 0.1 to change imediatley to standby temperature. Defaults to 30
#idle_to_powerdown_time: 300       # Time in seconds from being parked to setting temperature to 0. Use something like 86400 to wait 24h if you want to disable. Defaults to 600
lazy_home_when_parking: 1           # (default: 0 - disabled) - When set to 1, will home unhomed XY axes if needed and will not move any axis if already homed and parked. 2 Will also home Z if not homed.
extra_extrude_mm: 0.25


[tool 3]
tool_group: 0                     # Must be used and configured before this tool
extruder: extruder3
zone: 150,120
park: 188,327
meltzonelength: 18 #18                 # Defaults to 0
idle_to_standby_time: 0.1          # Time in seconds from being parked to setting temperature to standby the temperature above. Use 0.1 to change imediatley to standby temperature. Defaults to 30
#idle_to_powerdown_time: 300       # Time in seconds from being parked to setting temperature to 0. Use something like 86400 to wait 24h if you want to disable. Defaults to 600
lazy_home_when_parking: 1           # (default: 0 - disabled) - When set to 1, will home unhomed XY axes if needed and will not move any axis if already homed and parked. 2 Will also home Z if not homed.
extra_extrude_mm: 0.25


[tool 4]
tool_group: 0                     # Must be used and configured before this tool
extruder: extruder4
zone: 150,120
park: 243.7,327.9
meltzonelength: 18 #18                 # Defaults to 0
idle_to_standby_time: 0.1          # Time in seconds from being parked to setting temperature to standby the temperature above. Use 0.1 to change imediatley to standby temperature. Defaults to 30
#idle_to_powerdown_time: 300       # Time in seconds from being parked to setting temperature to 0. Use something like 86400 to wait 24h if you want to disable. Defaults to 600
lazy_home_when_parking: 1           # (default: 0 - disabled) - When set to 1, will home unhomed XY axes if needed and will not move any axis if already homed and parked. 2 Will also home Z if not homed.
extra_extrude_mm:0.25

[tool 5]
tool_group: 0                     # Must be used and configured before this tool
extruder: extruder5
zone: 150,120
park: 299.4,328.1
meltzonelength: 18 #18                 # Defaults to 0
idle_to_standby_time: 0.1          # Time in seconds from being parked to setting temperature to standby the temperature above. Use 0.1 to change imediatley to standby temperature. Defaults to 30
#idle_to_powerdown_time: 300       # Time in seconds from being parked to setting temperature to 0. Use something like 86400 to wait 24h if you want to disable. Defaults to 600
lazy_home_when_parking: 1           # (default: 0 - disabled) - When set to 1, will home unhomed XY axes if needed and will not move any axis if already homed and parked. 2 Will also home Z if not homed.
extra_extrude_mm: 0.25
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

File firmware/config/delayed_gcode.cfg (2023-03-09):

[delayed_gcode CHECK_AND_SET_TC_ERROR]
initial_duration: 1
gcode:
	CHECK_TOOLCHANGER_SWITCHES T={printer.save_variables.variables.tool_current}


[delayed_gcode GET_CURRENT_TOOL_FROM_SENSORS]
initial_duration: 2
gcode:
	GET_CURRENT_TOOL_FROM_SENSORS
	
[delayed_gcode CHECK_TOOLCHANGER_STATE]
initial_duration: 5
gcode:
	{% if printer["gcode_macro TOOLCHANGER_STATE"].tc_error_state|int == 1 %}
		SYNC_TOOLCHANGER_STATE
		#DISPLAYTOOL T=-2
	{% endif %}
	
#[delayed_gcode AUTO_DRIVER_FAN_START]
#initial_duration: 2
#gcode:
	#CONTROLLER_FAN_START
	
[delayed_gcode SET_INITIAL_SERVO_STATUS]
initial_duration: 1
gcode:
	#SERVO_TURN_ON
    {% if printer.save_variables.variables.tool_current >= 0 %}
        CLAMP_UP
    {% else %}
        CLAMP_DOWN
    {% endif %}

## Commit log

2023-01-10 Initial STL File Upload
    [carriage_left.stl, carriage_right.stl, dock_body.stl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]
2023-03-09 CAD Uploaded + Redesigned Dock + Dragon Tool Mounts
    [adaptive_bed_mesh.cfg, delayed_gcode.cfg, dock_wiper_bin.stl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]
2023-03-09 Firmware Uploaded + Credit for CAD Model
2023-04-10 Added link for the probe_multi_axis.py file
